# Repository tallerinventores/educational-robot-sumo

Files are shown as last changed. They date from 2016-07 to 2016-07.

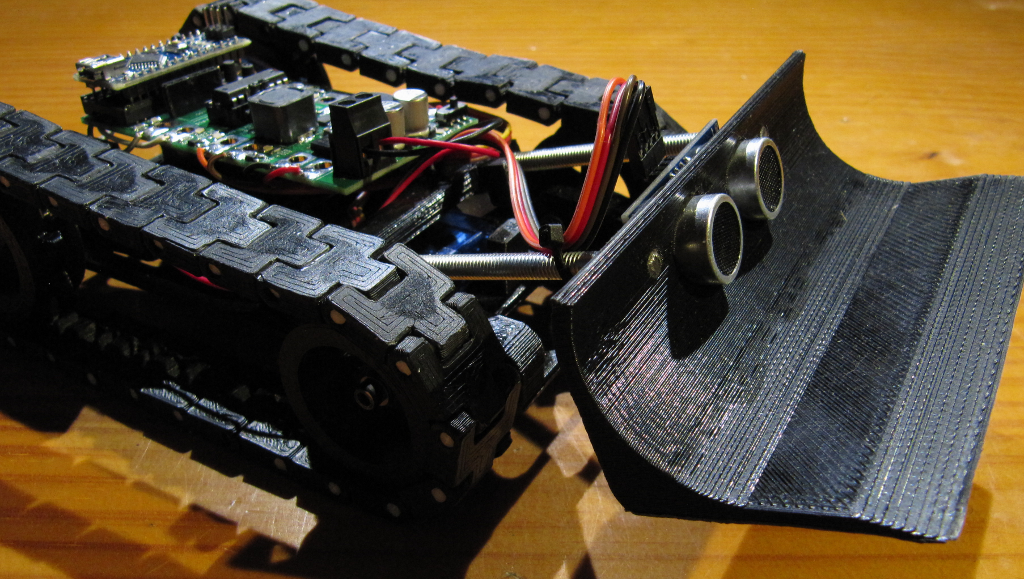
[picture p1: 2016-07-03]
img/photo-ers-7.png

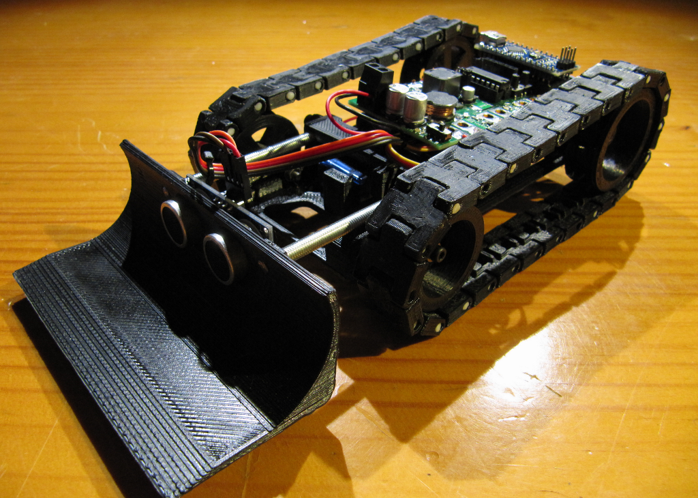
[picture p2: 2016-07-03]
img/photo-ers-4.png

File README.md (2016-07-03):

# educational-robot-sumo #

> Autonomous sumo-like robot for educational use  

* * *

## Resumen ##

Robot autónomo tipo sumo diseñado por los alumnos de la actividad de robótica
[Taller de Inventores](http://tallerinventores.github.io/). Ha sido desarrollado
y optimizado para impresión 3D y pensando en su bajo coste y facilidad de
montaje y uso.

## Instalación ##

En esta sección se cubre la instalación de software y hardware para el montaje
recomendado, mediante [Arduino](http://www.arduino.cc/).

### Requerimientos de software ###

Para poder usar Arduino (v1.6+) con el código fuente proporcionado, son
necesarias la librerías [NewPing](http://playground.arduino.cc/Code/NewPing) y
Servo (incluida en el IDE de Arduino). Para generar los archivos aptos para la
impresora 3D desde los archivos `.stl` será necesario adicionalmente un software
para esta función, como puede ser [Slic3r](http://slic3r.org/).

### Requerimientos de hardware ###

Será necesario para su montaje y uso cuatro pilas tipo AA, dos motores con
reductora en miniatura, un sensor de distancia por ultrasonidos HC-SR04, un
servomotor tipo 9g con sus correspondientes accesorios (tornillos y cuernos) y
una placa Robgednaut Zond con un Arduino Nano o compatible. El robot está
optimizado para usar el servo **TowerPro SG90**. Adicionalmente hará falta
tornillería variada de métrica tres y cinco. Se recomienda un macho de las
mismas métricas.  

## Uso ##

Instrucciones de montaje y puesta en marcha.

### Montaje del robot ###

1.  Imprimir una unidad de los archivos `shovel-mount.stl`, `shovel.stl` y
    `base.stl`. Imprimir dos unidades de `wheel.stl`, `driving-wheel.stl` y
    `motor-cover.stl`. Imprimir cincuenta y dos unidades de `track-link.stl`.
    Puede ser necesario repasar las piezas impresas con el fin de eliminar
    rebabas.  
2.  Insertar un pasador de 3mm (trozo de filamento) de veinte milímetros de
    largo para unir cada pareja de eslabones (_track-link_), haciendo dos
    cadenas cerradas de la misma longitud.
3.  Montar el servo sobre el chasis del robot (_base_) y fijarlo usando uno de
    los tornillos de montaje del servo. Colocar el cuerno y asegurarse de que el
    ángulo de reposo está orientado hacia la parte delantera. Atornillar el
    cuerno con el tornillo proporcionado por el servo.
4.  Fijar el portapilas sobre la base, atornillándolo con dos tornillos de
    métrica tres por seis, roscando sobre el portapilas.
5.  Con dos tramos de varilla roscada de métrica cinco y setenta milímetros de
    largo, roscar un extremo sobre la pala (_shovel_), con la rosca previamente
    hecha. Colocar el sensor de distancia en su sitio e insertar el conjunto
    sobre el soporte (_shovel-mount_).
6.  Crear los dos ejes delanteros a partir de dos tornillos de métrica tres por
    treinta con caña. Insertar en el tornillo dos arandelas planas, la rueda
    loca (_wheel_), otras dos arandelas planas, fijar con tuerca y contratuerca,
    de forma que permita girar libremente la rueda, insertar una arandela plana
    y colocar en la ranura del eje delantero. Fijar con otra arandela en el
    extremo contrario y una tuerca sin apretar. El conjunto del eje delantero
    debe poder correr libremente por la guía.
7.  Presentar el conjunto de la pala sobre la estructura principal y fijarla a
    la misma con dos tornillos de métrica tres por dieciséis, habiendo creado
    rosca sobre el soporte de la pala previamente.
8.  Insertar el eje del motor en las ruedas motrices (_driving-wheel_) y fijarlo
    con un tornillo de métrica tres por seis sobre la cara plana del eje del
    motor. Crear previamente la rosca en el agujero para el prisionero de la
    rueda.
9.  Colocar los dos motores con las ruedas motrices sobre la estructura
    principal, y sujetar apretando las tapas (_motor-cover_) contra la base,
    roscando dos tornillos de métrica tres por dieciséis en la rosca previamente
    realizada.
10. Alinear las ruedas de ambos extremos si fuera necesario, ajustando el
    tornillo prisionero de la rueda motriz.
11. Colocar en su sitio las orugas, asegurando que coinciden correctamente.
    Tensar levemente la oruga con el eje delantero y fijarlo en el sitio.
12. Realizar las uniones eléctricas y la gestión de cables pertinente.

### Conexión eléctrica ###

Este proyecto usa [Robgednaut](http://akornsys-rdi.github.io/robgednaut/) Zond
como placa de conexionado, si no dispones de ella puedes ver su esquema de
conexiones en la página oficial.  

Las alimentaciones para todos los dispositivos las provee la placa de control.
El cable de dato del servomotor se conecta a A, las señales del sensor de
distancia ECHO y TRIGGER se conectan a B y D respectivamente. Los motores de
cada lado van conectados a un canal de la salida para motores, respetando su
polaridad.

### Firmware ###

El Arduino deberá tener cargado el firmware incluido en la carpeta `src` de este
repositorio.  

### Bugs ###

Se han observado los siguientes problemas:  

-   Es necesario sellar los pasadores a los eslabones para evitar que éstos se
    salgan durante el movimiento del robot.  
-   Para ser robot de sumo le faltan los sensores de proximidad que detectan el
    borde del tatami.  

## Enlaces externos ##

Este proyecto también está presente en:  

-   [Thingiverse](http://www.thingiverse.com/thing:1656919).  

## Créditos ##

Proyecto realizado por Taller de Inventores 2016, representado por:  

-   kwendenarmo <kwendenarmo@akornsys-rdi.net>  

Alumnos del Centro de Formación Padre Piquer:  

-   A, Daniel  
-   L, Mario  
-   L, Omar  
-   L, Tarek

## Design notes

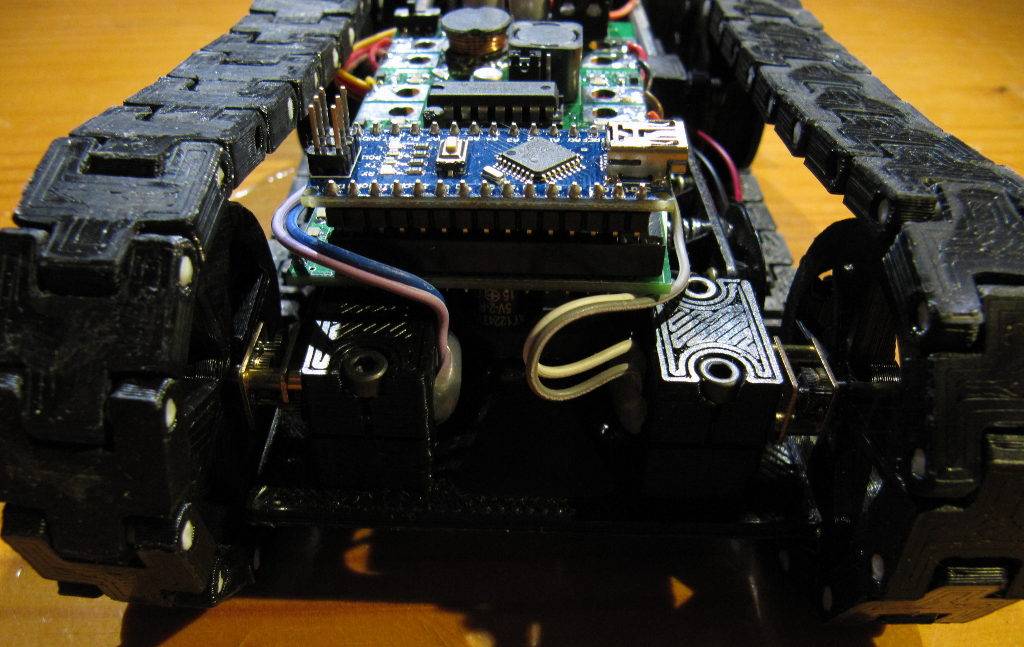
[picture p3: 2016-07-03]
img/photo-ers-5.png

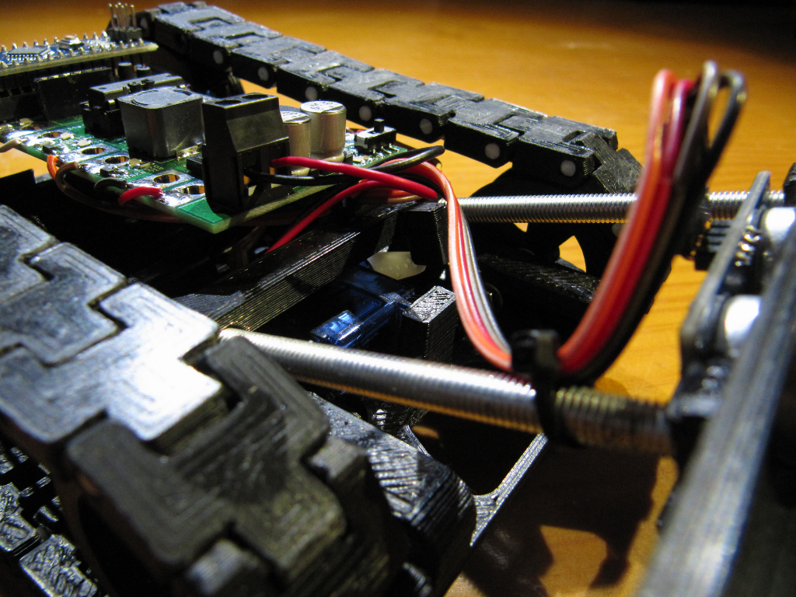
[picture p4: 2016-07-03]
img/photo-ers-2.png

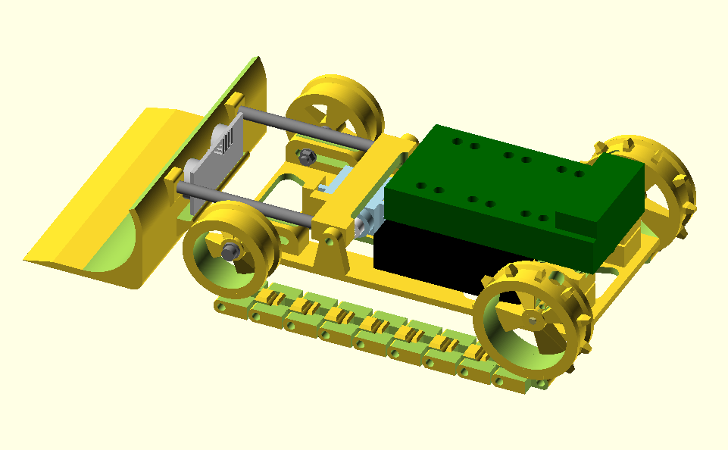
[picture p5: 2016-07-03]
img/render.png

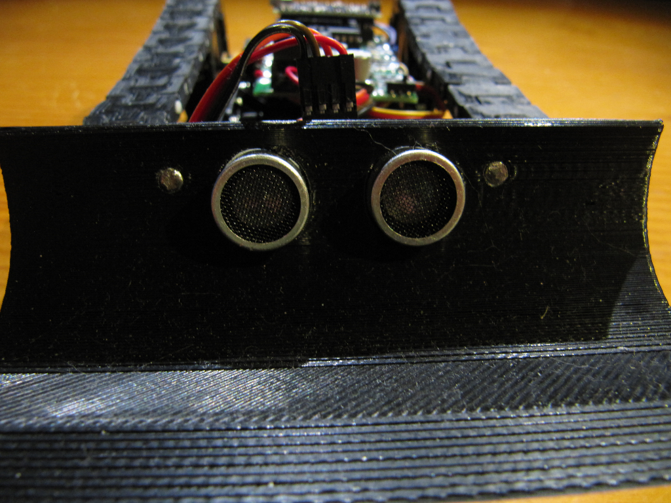
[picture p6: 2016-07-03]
img/photo-ers-3.png

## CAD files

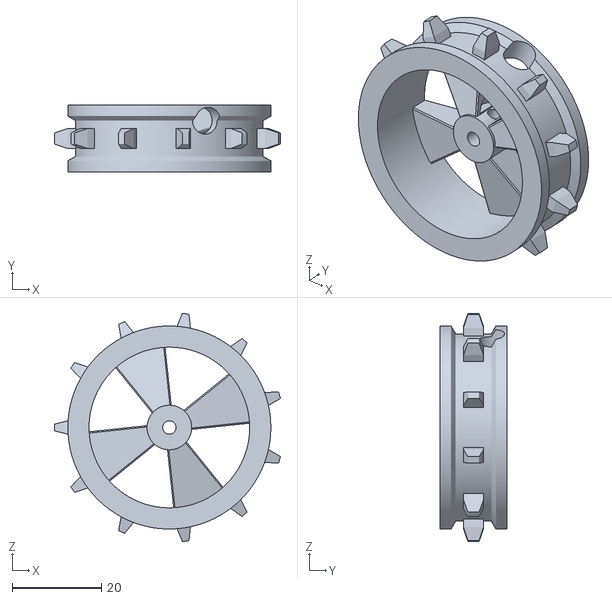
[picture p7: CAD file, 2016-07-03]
3d/driving-wheel.stl
50.7 x 15.0 x 51.2

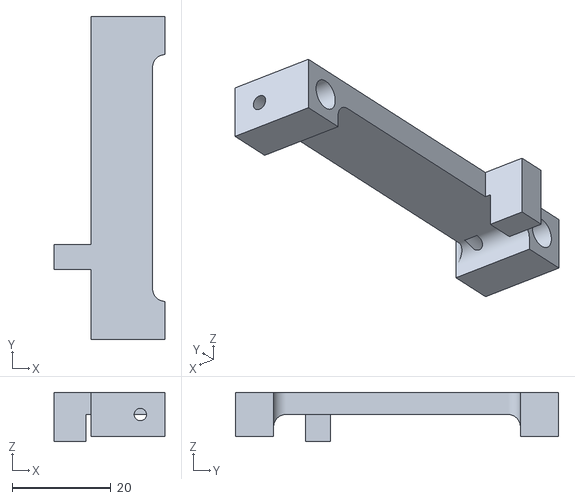
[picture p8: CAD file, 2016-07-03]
3d/shovel-mount.stl
22.5 x 65.5 x 10.0

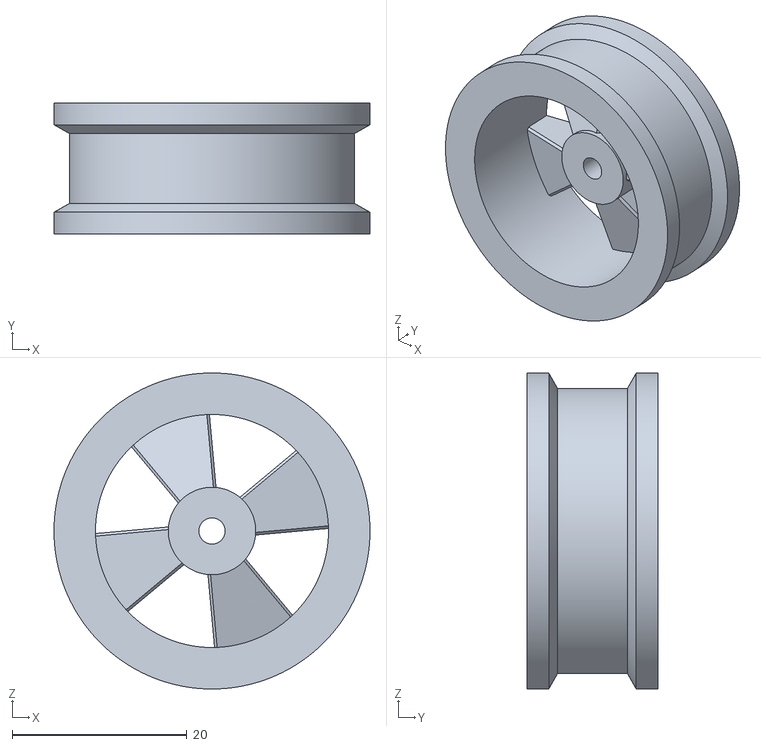
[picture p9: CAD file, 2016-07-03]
3d/wheel.stl
36.2 x 15.0 x 36.2

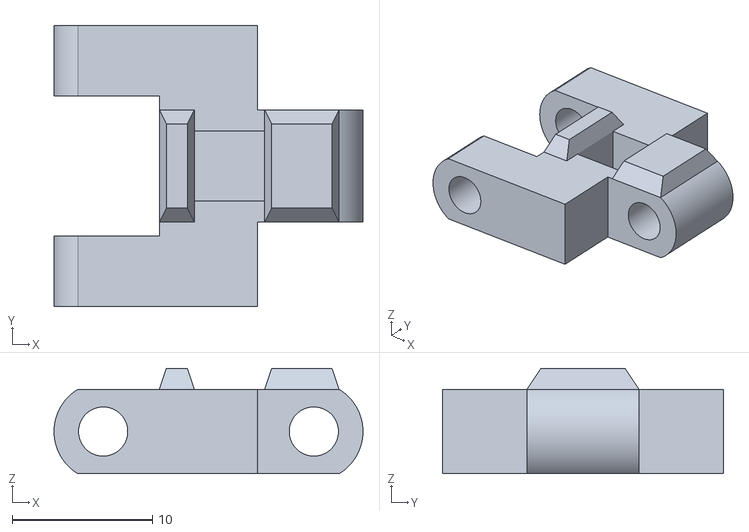
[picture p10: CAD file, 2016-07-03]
3d/track-link.stl
22.0 x 20.0 x 7.50

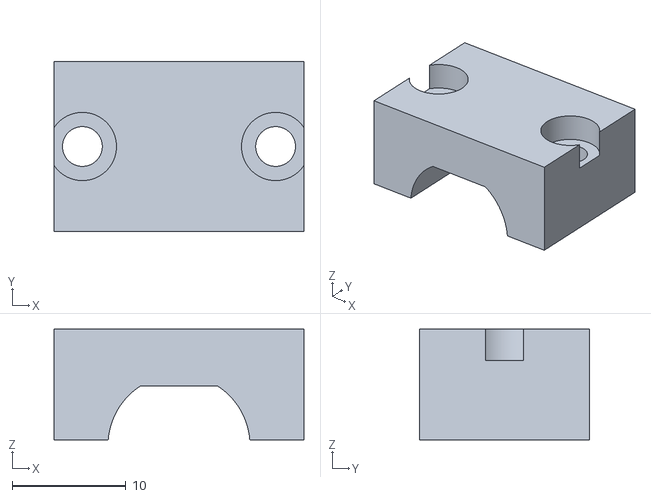
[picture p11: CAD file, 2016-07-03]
3d/motor-cover.stl
22.0 x 15.0 x 9.76

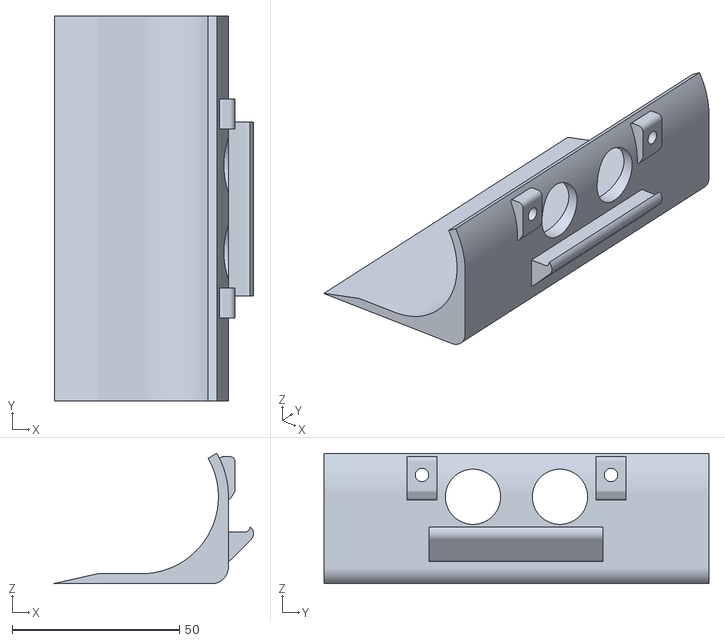
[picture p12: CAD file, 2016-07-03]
3d/shovel.stl
59.5 x 115.0 x 39.0

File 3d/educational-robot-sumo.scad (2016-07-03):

/* {{{ %%SECTION_HEADER%%
 * * * *
 * This header information is automatically generated by KodeUtils.
 *
 * File 'educational-robot-sumo.scad' edited by kwendenarmo,
 * last modified: 2016-07-03.
 * This file is part of 'educational-robot-sumo' package, please see
 * the readme files for more information about this file and this package.
 *
 * Copyright (C) 2016 by kwendenarmo <kwendenarmo@akornsys-rdi.net>
 * Released under the GNU GPLv3
 *
 *    This program is free software: you can redistribute it and/or modify
 *    it under the terms of the GNU General Public License as published by
 *    the Free Software Foundation, either version 3 of the License, or
 *    (at your option) any later version.
 *
 *    This program is distributed in the hope that it will be useful,
 *    but WITHOUT ANY WARRANTY; without even the implied warranty of
 *    MERCHANTABILITY or FITNESS FOR A PARTICULAR PURPOSE.  See the
 *    GNU General Public License for more details.
 *
 *    You should have received a copy of the GNU General Public License
 *    along with this program.  If not, see <http://www.gnu.org/licenses/>.
 *
 * * * *
 * %%EOS_HEADER%% }}}
 */

$fn=360;

/*
 *  Tornillos
 *  -   Eje delantero 2x M3x30 + 2 arandela plana + 2 arandela plana + 2 tuerca + 1 arandela plana + 1 arandela plana + 1 tuerca
 *  -   Sujeción soporte pala 2x M3x16
 *  -   Varillas soporte pala 2x M5x70
 *  -   Portapilas 2x M3x6
 *  -   Prisionero ruedas motrices 2x M3x6
 *  -   Sujeciones tapas motor 4x M3x16
 *  -   Tornillo plastico cuerno servo
 *  -   Tornillo plastico fijación servo
 */

translate([-10,20,12.5]) base();
translate([-60,0,23]) pala();
translate([-28,34.8,33.6]) rotate([-90,0,90]) hcsr04();
translate([37.25,0,29.5]) soporte_pala();
translate([37.25,45,21.75]) rotate([90,0,0]) servo9g(180);
translate([0,17.5,21.07665]) rotate([0,0,180]) wheel(9);
translate([0,8.75,21.07665]) rotate([0,0,180]) eje_delantero();
translate([130,17.5,25.76035]) rotate([0,0,180]) driving_wheel(11);
translate([130,18.5,25.76035]) motor();
translate([119,29,25.75]) tapa_motor();
translate([0,97.5,21.07665]) wheel(9);
translate([0,106.25,21.07665]) eje_delantero();
translate([130,97.5,25.76035]) driving_wheel(11);
translate([130,96.5,25.76035]) rotate([0,0,180]) motor();
translate([119,71,25.75]) tapa_motor();
for (i=[0:15:130]) {
    for(j=[0:95:95]) {
        translate([i,j,0]) track_link();
    }
}
translate([52.5,28.5,16]) rotate([0,0,0]) portapilas();
translate([145,33.65,37]) rotate([0,0,90]) roben_zond();

module base() {
    difference() {
        union() {
            //base
            cube([155,75,3]);
            //corredera tensor izquierda
            translate([6,4.2,8.57665]) hull() {
                rotate([-90,0,0]) cylinder(r=6, h=10);
                translate([20,0,0]) rotate([-90,0,0]) cylinder(r=6, h=10);
                translate([-6,0,-6]) cube([32,10,6]);
            }
            //corredera tensor derecha
            translate([6,60.8,8.57665]) hull() {
                rotate([-90,0,0]) cylinder(r=6, h=10);
                translate([20,0,0]) rotate([-90,0,0]) cylinder(r=6, h=10);
                translate([-6,0,-6]) cube([32,10,6]);
            }
            //soporte motor izquierdo
            translate([129,9,3]) cube([22,15,9.76035]);
            //soporte motor derecho
            translate([129,51,3]) cube([22,15,9.76035]);
            //soporte pala izquierdo
            translate([47.25,0,17]) hull() {
                rotate([-90,0,0]) cylinder(r=4, h=4.5);
                translate([-7,0,-15]) cube([14,4.5,1]);
            }
            //soporte pala derecho
            translate([47.25,70.5,17]) hull() {
                rotate([-90,0,0]) cylinder(r=4, h=4.5);
                translate([-7,0,-15]) cube([14,4.5,1]);
            }
            //encajes servo
            translate([53.5,36.5,0]) cube([5,4,15.5]);
            translate([21.75,29.5,0]) cube([5,11,17]);
        }
        union() {
            //esquina delantera izquierda
            difference() {
                translate([-1,-1,-1]) cube([8,5,5]);
                hull() {
                    translate([0.5,3.5,0]) cylinder(r=0.5, h=3);
                    translate([0.5,5,0]) cylinder(r=0.5, h=3);
                    translate([7,0.5,0]) cylinder(r=0.5, h=3);
                    translate([7,5,0]) cylinder(r=0.5, h=3);
                }
            }
            //esquina delantera derecha
            difference() {
                translate([-1,71,-1]) cube([8,5,5]);
                hull() {
                    translate([0.5,71.5,0]) cylinder(r=0.5, h=3);
                    translate([0.5,70,0]) cylinder(r=0.5, h=3);
                    translate([7,74.5,0]) cylinder(r=0.5, h=3);
                    translate([7,70,0]) cylinder(r=0.5, h=3);
                }
            }
            //guia corredera tensor izquierda
            translate([6,3.2,8.57665]) hull() {
                rotate([-90,0,0]) cylinder(r=1.75, h=12);
                translate([20,0,0]) rotate([-90,0,0]) cylinder(r=1.75, h=12);
            }
            //guia corredera tensor derecha
            translate([6,59.7,8.57665]) hull() {
                rotate([-90,0,0]) cylinder(r=1.75, h=12);
                translate([20,0,0]) rotate([-90,0,0]) cylinder(r=1.75, h=12);
            }
            //reposa-soporte pala izquierdo
            translate([0,9.25,17]) rotate([0,90,0]) cylinder(r=3.5, h=30);
            //reposa-soporte pala derecho
            translate([0,65.75,17]) rotate([0,90,0]) cylinder(r=3.5, h=30);
            //agujero tornillo pivotante pala
            translate([47.25,-1,17]) rotate([-90,0,0]) cylinder(r=1.75, h=77);
            //cajeado servo
            translate([55.625,35,9.25]) rotate([-90,0,0]) cylinder(r=0.75, h=6);
            translate([24,33.5,3]) cube([3,3,13]);
            //hueco motor
            translate([140,8,25.76035-12.5]) difference() {
                rotate([-90,0,0]) cylinder(r=6.25, h=59); //motor
                union() {
                    translate([-6.25,-1,5.25]) cube([12.5,61,3]);
                    translate([-6.25,-1,-8.25]) cube([12.5,61,3]);
                }
            }
            //agujeros tapa motor izquierdo
            translate([131.5,16.5,3]) cylinder(r=1.25, h=11);
            translate([148.5,16.5,3]) cylinder(r=1.25, h=11);
            //agujeros tapa motor derecho
            translate([131.5,58.5,3]) cylinder(r=1.25, h=11);
            translate([148.5,58.5,3]) cylinder(r=1.25, h=11);
            //agujeros portapilas
            translate([66.4,37.5,-1]) union() {
                cylinder(r=1.25, h=6);
                translate([54.7,0,0]) cylinder(r=1.25, h=6);
            }
            //aligerar base
            translate([6,50,-1]) hull() {
                cylinder(r=4, h=5);
                translate([0,-25,0]) cylinder(r=4, h=5);
                translate([10,-5,0]) cylinder(r=4, h=5);
                translate([10,-20,0]) cylinder(r=4, h=5);
            }
            translate([147,30,-1]) hull() {
                cylinder(r=4, h=5);
                translate([0,15,0]) cylinder(r=4, h=5);
                translate([-15,10,0]) cylinder(r=4, h=5);
                translate([-15,5,0]) cylinder(r=4, h=5);
            }
            translate([30,21.5,-1]) hull() {
                cylinder(r=6, h=5);
                translate([50,0,0]) cylinder(r=6, h=5);
            }
            translate([30,53.5,-1]) hull() {
                cylinder(r=6, h=5);
                translate([50,0,0]) cylinder(r=6, h=5);
            }
            translate([105,10,-1]) hull() {
                cylinder(r=4, h=5);
                translate([15,0,0]) cylinder(r=4, h=5);
                translate([-15,22,0]) cylinder(r=4, h=5);
                translate([0,22,0]) cylinder(r=4, h=5);
            }
            translate([90,43,-1]) hull() {
                cylinder(r=4, h=5);
                translate([15,0,0]) cylinder(r=4, h=5);
                translate([15,22,0]) cylinder(r=4, h=5);
                translate([30,22,0]) cylinder(r=4, h=5);
            }
        }
    }
}
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

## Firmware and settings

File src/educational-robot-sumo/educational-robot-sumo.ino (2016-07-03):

#include <NewPing.h>
NewPing sonar(11, 3, 100);
#include <Servo.h>
Servo pala;

#define HALT 0
#define FORWARD 1
#define BACKWARD 2
#define TURN_LEFT 3
#define TURN_RIGHT 4
#define LEFT 1
#define RIGHT 2
#define BOTH 3

void setup() {
    //pulsadores
    pinMode(A2, INPUT);
    pinMode(A3, INPUT);
    //LED
    pinMode(12, OUTPUT);
    pinMode(A0, OUTPUT);
    pinMode(A1, OUTPUT);
    //servo
    pala.attach(2);
    pala.write(180);
    //motores
    pinMode(8, OUTPUT);
    pinMode(7, OUTPUT);
    pinMode(10, OUTPUT);
    pinMode(5, OUTPUT);
    pinMode(9, OUTPUT);
    pinMode(6, OUTPUT);
    moveRobot(HALT, BOTH, 0, 0);
    digitalWrite(7, HIGH);
    digitalWrite(8, HIGH);
    //start
    while (digitalRead(A3) == LOW) {
        digitalWrite(12, HIGH);
        digitalWrite(A0, HIGH);
        digitalWrite(A1, HIGH);
        delay(50);
        digitalWrite(12, LOW);
        digitalWrite(A0, LOW);
        digitalWrite(A1, LOW);
        delay(50);
    }
    delay(1000);
    tone(4, 400, 100);
    digitalWrite(12, HIGH);
    delay(1000);
    tone(4, 800, 100);
    digitalWrite(A0, HIGH);
    delay(1000);
    tone(4, 1600, 250);
    digitalWrite(A1, HIGH);
    delay(250);
    noTone(4);
}

void loop() {
    if (search()) {
        attack();
        retreat();
    }
}

unsigned char search() {
    unsigned char stat = 0;
    static unsigned char lastStage = 0;

    digitalWrite(A1, LOW);
    digitalWrite(A0, HIGH);
    digitalWrite(12, LOW);
    if (findOpponent()) stat = 1;
    else {
        if (lastStage == 0) {
            lastStage = 1;
            moveRobot(TURN_LEFT, BOTH, 255, 1000);
        }
        else if (lastStage == 1) {
            lastStage = 2;
            moveRobot(TURN_RIGHT, BOTH, 255, 1000);
        }
        else if (lastStage == 2) {
            lastStage = 3;
            moveRobot(TURN_RIGHT, BOTH, 255, 1000);
        }
        else if (lastStage == 3) {
            lastStage = 0;
            moveRobot(TURN_LEFT, BOTH, 255, 1000);
        }
    }
    digitalWrite(A0, LOW);
    return stat;
}

void attack() {
    digitalWrite(A1, HIGH);
    digitalWrite(A0, LOW);
    digitalWrite(12, LOW);
    moveRobot(FORWARD, BOTH, 255, 6000);
    //levantar y bajar servo 4x
    for (int i = 0; i < 5; i++){
        pala.write(150);
        delay(250);
        pala.write(180);
        delay(250);
    }
    digitalWrite(A1, LOW);
}

void retreat() {
    digitalWrite(A1, LOW);
    digitalWrite(A0, LOW);
    digitalWrite(12, HIGH);
    pala.write(150);
    moveRobot(BACKWARD, BOTH, 255, 6000);
    pala.write(180);
    digitalWrite(12, LOW);
}

void moveRobot(unsigned char course, unsigned char motor, unsigned char value, unsigned int distance) {
    switch (motor){
      case LEFT:
        if (course == HALT) {
            digitalWrite(5, LOW);
            digitalWrite(10, LOW);
        }
        else if (course == FORWARD) {
            digitalWrite(10, LOW);
            analogWrite(5, value);
            delay(distance);
            digitalWrite(5, LOW);
        }
        else if (course == BACKWARD) {
            digitalWrite(5, LOW);
            analogWrite(10, value);
            delay(distance);
            digitalWrite(10, LOW);
        }
        break;
      case RIGHT:
        if (course == HALT) {
            digitalWrite(6, LOW);
            digitalWrite(9, LOW);
        }
        else if (course == FORWARD) {
            digitalWrite(9, LOW);
            analogWrite(6, value);
            delay(distance);
            digitalWrite(6, LOW);
        }
        else if (course == BACKWARD) {
            digitalWrite(6, LOW);
            analogWrite(9, value);
            delay(distance);
            digitalWrite(9, LOW);
        }
        break;
      case BOTH:
        if (course == HALT) {
            digitalWrite(5, LOW);
            digitalWrite(10, LOW);
            digitalWrite(6, LOW);
            digitalWrite(9, LOW);
        }
        else if (course == FORWARD) {
            digitalWrite(10, LOW);
            analogWrite(5, value);
            digitalWrite(9, LOW);
            analogWrite(6, value);
            delay(distance);
            digitalWrite(5, LOW);
            digitalWrite(6, LOW);
        }
        else if (course == BACKWARD) {
            digitalWrite(5, LOW);
            analogWrite(10, value);
            digitalWrite(6, LOW);
            analogWrite(9, value);
            delay(distance);
            digitalWrite(10, LOW);
            digitalWrite(9, LOW);
        }
        else if (course == TURN_LEFT) {
            digitalWrite(5, LOW);
            analogWrite(10, value);
            digitalWrite(9, LOW);
            analogWrite(6, value);
            delay(distance);
            digitalWrite(10, LOW);
            digitalWrite(6, LOW);
        }
        else if (course == TURN_RIGHT) {
            digitalWrite(10, LOW);
            analogWrite(5, value);
            digitalWrite(6, LOW);
            analogWrite(9, value);
            delay(distance);
            digitalWrite(5, LOW);
            digitalWrite(9, LOW);
        }
    }
}

unsigned char findOpponent() {
    unsigned char target = 0;
    unsigned int dist = 0;

    dist = sonar.ping_cm();
    if ((dist <= 50) && (dist >= 3)) target = 1;
    return target;
}
